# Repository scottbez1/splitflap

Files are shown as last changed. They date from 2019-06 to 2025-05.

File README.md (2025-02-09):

# Split-Flap Display

This is a DIY ESP32-based [split-flap display](https://en.wikipedia.org/wiki/Split-flap_display), optimized for easy assembly at home in small quantities but able to be scaled up to large affordable displays.

animated rendering






The [splitflap community Discord server](https://discord.com/invite/wgehm3PcrC) is the best place to keep up with the latest changes or ask questions about the project!

Want to help support development or just say "thanks"? Consider a one-time or monthly sponsorship:

| [:heart: Sponsor scottbez1 on GitHub](https://github.com/sponsors/scottbez1) |
|---|

<a href="https://www.youtube.com/watch?v=UAQJJAQSg_g" target="_blank">
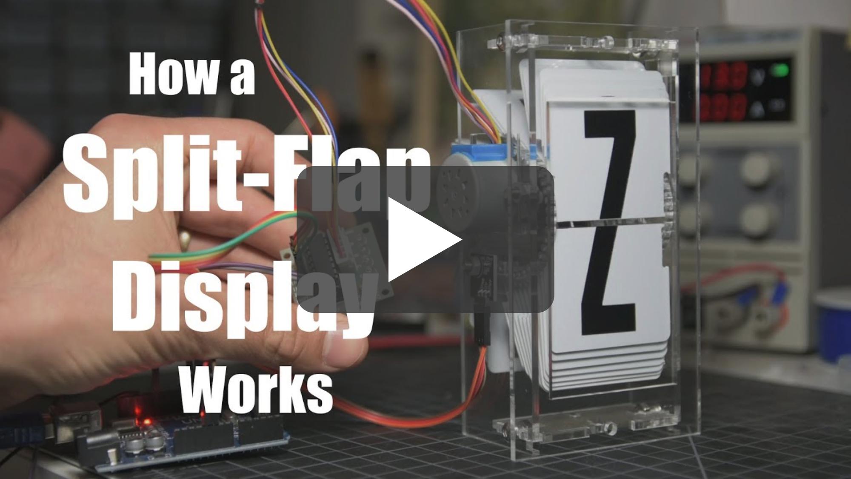
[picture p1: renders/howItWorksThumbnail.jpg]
  
</a>

**Using this project in a commercial setting or for paid client work?** Go right ahead - it's open source (just make sure to follow the terms of the Apache License)! I would, however, ask that you consider [sponsoring the project](https://github.com/sponsors/scottbez1). I've been developing and maintaining this project in my free time for over 10 years, and I'd love to continue working on it. Sponsorships allow me to pay for prototypes and development tools that make this project possible. Unlike pure software projects, every iteration has real hardware costs; sponsorships allow me to keep iterating and improving the project faster. Thank you!

# Current Status
[You can download the **latest stable releases** of the hardware designs from the official 'releases' page.](https://github.com/scottbez1/splitflap/releases)

Releases have been tested and used to produce working units, but as this is a continuously evolving open-source project, there may always be minor issues and/or incomplete documentation from time to time.

Here's a video of a large 108-module display powered by 18 Chainlink Driver boards and a Chainlink Base:

Video: animations on 108-module display (https://youtu.be/g9EPabcxBsM)

## Stable v2 Mechanical Release
As of 2025-01-19, the v2 refresh of the mechanical and sensor design is considered stable and recommended for new builds.

**Here's what's new in v2:**

- **52 flaps per module** for more character/symbol options
- **New printed flap design ("Epilogue")** with 52 flaps per set (see animation above), including several color-block flaps
- **Updated enclosure** and mechanical parts (laser-cut) to accomodate 52 flaps
  - Motor wires now exit downward for less awkward wiring!
- **New sensor PCB** that's easier to assemble and includes an LED for checking the magnet status
- **Software-configurable calibration** rather than mechanical sensor adjustment

**But many things are staying the same for easy upgrades/compatibility:**
- No change to flap dimensions!
- No changes to Chainlink Driver, Chainlink Buddy boards, or system architecture!
- 40-flap modules are still an officially supported option!
- Open source, as always!
- v0 parts (sensor kits) will continue to be stocked at Bezek Labs through mid-2025; don't worry if you haven't finished your build yet, the old sensor kits aren't going away for a little while!

I'd love to hear your thoughts and questions about this project, and happy to incorporate any feedback you might have into these designs! Please feel free (and encouraged) to [open GitHub issues](https://github.com/scottbez1/splitflap/issues/new), email me directly, reach out [on Bluesky](https://bsky.app/profile/scottbez1.bsky.social), and [get involved](https://github.com/scottbez1/splitflap/pulls) in the open source development and let's keep chatting and building together!

# Build Your Own
If you have any questions, please don't hesitate to ask in the [community Discord server](https://discord.gg/Hxnftc8PyW)!

* [**Documentation Index**](/docs/DocumentationIndex.md)
* [**Ordering guide (the "easy" route) v2**](/docs/v2/OrderingEasy.md)
* [**Comprehensive ordering guide**](/docs/v2/OrderingComplete.md)
* [**Chainlink Driver Electronics User Guide**](/docs/ElectronicsGuide.md)
* [**Assembly instructions v2**](/docs/v2/Assembly.md)
* [**Latest stable releases**](https://github.com/scottbez1/splitflap/releases)

# Table of Contents
- [Design Overview](#design-overview)
  - [Mechanical](#mechanical)
    - [Combined front panel (script)](#combined-front-panel-script)
    - [Flap font/sticker generator (script)](#flap-fontsticker-generator-script)
  - [Electronics](#electronics)
    - [Sensor PCBs](#sensor-pcbs-1-per-module)
    - [Chainlink Driver](#chainlink-driver-1-per-6-modules)
    - [Chainlink Buddy \[T-Display\]](#chainlink-buddy-t-display-1-for-entire-display)
    - [Advanced items](#advanced-items)
      - [Chainlink Buddy \[Breadboard\]](#chainlink-buddy-breadboard-1-for-entire-display-alternative-to-t-display)
      - [Chainlink Base](#chainlink-base-1-for-entire-display-large-displays)
    - [Older designs](#older-designs)
      - [Classic controller](#classic-controller-electronics-deprecated)
    + [Miscellaneous Tools](#miscellaneous-tools)
      - [3D Printed Tools](#3d-printed-tools)
      - [Chainlink Driver Tester](#chainlink-driver-tester)
  * [Code](#code)
    + [Firmware](#firmware)
    + [Computer Control Software](#computer-control-software)
- [Contributing/Modifying](#contributingmodifying)
  * [3D Design](#3d-design)
  * [Electronics Design](#electronics-design)

# Design Overview

## Mechanical
The mechanical/structural components are made from laser-cut 3mm MDF or acrylic, and held together with M4 bolts and nuts. The design is parametric and built using OpenSCAD. See below for more info on rendering/modifying the design.

You can view an interactive 3d model of the design [here](https://scottbez1.github.io/splitflap/embed.html?branch=master).

The v2 mechanical design officially supports variants with 52 flaps (perfect for use with the new ["Epilogue" printed flaps](https://bezeklabs.etsy.com/listing/1685633114/)) and 40 flaps. But you can always modify the design to customize it further.

### v2 (52-flap module option - recommended)
2d laser cut rendering

Instructions: [v2 assembly guide](/docs/v2/Assembly.md)

Module dimensions: 

Latest auto-generated (untested!) artifacts<sup>:warning:</sup>:
* For Ponoko 3mm MDF ([svg](https://s3.amazonaws.com/splitflap-artifacts/master/3d/3d_laser_vector-52-ponoko-3mm-mdf_1x.svg)) 
* For Ponoko 3mm acrylic ([svg](https://s3.amazonaws.com/splitflap-artifacts/master/3d/3d_laser_vector-52-ponoko-3mm-acrylic_1x.svg)) 
* For generic material (0.18mm kerf correction) ([svg](https://s3.amazonaws.com/splitflap-artifacts/master/3d/3d_laser_vector-52.svg))
* For Elecrow 3mm Wood ([zipped pdf](https://s3.amazonaws.com/splitflap-artifacts/master/3d/3d_laser_vector-52-elecrow-3mm-wood_1x.zip))
* For Elecrow 3mm Acrylic ([zipped pdf](https://s3.amazonaws.com/splitflap-artifacts/master/3d/3d_laser_vector-52-elecrow-3mm-acrylic_1x.zip))

<sup>:warning:</sup>For tested/stable/recommended artifacts, always use the [latest release](https://github.com/scottbez1/splitflap/releases) instead, as the links on this page will change over time.

### v2 (40-flap module option)
2d laser cut rendering

Instructions: [v2 assembly guide](/docs/v2/Assembly.md)

Module dimensions: 

Latest auto-generated (untested!) artifacts<sup>:warning:</sup>:
* For Ponoko 3mm MDF ([svg](https://s3.amazonaws.com/splitflap-artifacts/master/3d/3d_laser_vector-40-ponoko-3mm-mdf_1x.svg)) 
* For Ponoko 3mm acrylic ([svg](https://s3.amazonaws.com/splitflap-artifacts/master/3d/3d_laser_vector-40-ponoko-3mm-acrylic_1x.svg)) 
* For generic material (0.18mm kerf correction) ([svg](https://s3.amazonaws.com/splitflap-artifacts/master/3d/3d_laser_vector-52.svg))
* For Elecrow 3mm Wood ([zipped pdf](https://s3.amazonaws.com/splitflap-artifacts/master/3d/3d_laser_vector-40-elecrow-3mm-wood_1x.zip))
* For Elecrow 3mm Acrylic ([zipped pdf](https://s3.amazonaws.com/splitflap-artifacts/master/3d/3d_laser_vector-40-elecrow-3mm-acrylic_1x.zip))

<sup>:warning:</sup>For tested/stable/recommended artifacts, always use the [latest release](https://github.com/scottbez1/splitflap/releases) instead, as the links on this page will change over time.

### Combined front panel (script)
By default, the design will have a separate laser-cut faceplate for each individual module. For larger displays you may want to combine front panels into a single piece, and the repo has a script to help with this.

You can modify:
* Number of rows and columns
* Horizontal and vertical spacing/separation of modules
* Overall outer width and height of the panel

There are a lot of options; see the `--help` for explanations.

#### Example 1 - Laser cut 6x1

<a href="https://s3.amazonaws.com/splitflap-artifacts/master/3d/3d_front_panel-52-elecrow-3mm-acrylic-6x1.svg">

</a>

```
python3 3d/scripts/generate_combined_front_panel.py \
  --kerf-preset elecrow-3mm-acrylic \
  --num-flaps 52 \
  --cols 6 \
  --rows 1 \
  --spacing-x 0 \
  --spacing-y 0 \
  --frame-margin-x 0 \
  --frame-margin-y 0 \
  --center-mode module
```

#### Example 2 - CNC router 12x2, with frame margin
<a href="https://s3.amazonaws.com/splitflap-artifacts/master/3d/3d_front_panel-52-3.175-20x4margin-12x2.svg">

</a>

For CNC cutting, the script supports rendering a vector file optimized for thicker material (e.g. 6mm MDF) where only the bolt-holes will be through-cut. In this mode, the slots for the top/bottom enclosure pieces can be cut as ~4mm pockets so they aren't visible from the front face. The script automatically generates dog-bone shapes for these pocket cuts.

This example also demonstrates use of the --frame-margin-x and --frame-margin-y options to add an additional margin of 20mm horizontally and 4mm vertically to the front panel dimensions.

```
python3 3d/scripts/generate_combined_front_panel.py \
  --tool-diameter 3.175 \
  --num-flaps 52 \
  --cols 12 \
  --rows 2 \
  --spacing-x 0 \
  --spacing-y 0 \
  --frame-margin-x 20 \
  --frame-margin-y 4 \
  --center-mode module
```

### Flap font/sticker generator (script)
If you'd like to print your own flaps, or cut custom vinyl letter stickers, the project includes a script (`generate_fonts.py`) to generate vector design files, which is extremely configurable:

* Font for text
  * This is further customizable in `flap_fonts.scad` -- this is where font parameters are defined like the overall font scale, position offsets, and even per-character scale and position overrides in case you need to tweak particularly problematic letters (e.g. a really wide "W" or an "@" with too thin of a stroke).
* Character-set - which letters/numbers/symbols/colors are included and in what order
* Bleed - extends rendering past the borders of the flaps to compensate for slight misalignment of printing and cutting operations
* Keepout areas - option to highlight keepout violations for manual review, automatically clip them, or ignore them
* Rendering options:
    * Single-sided - useful for previewing how all letters will look on flaps
    * Front/back - for batch duplex printing, generate separate front-side and back-side files (e.g. sign shop printing on a flat sheet of PVC)
    * Side-by-side - for individual flap printing, each flap's front design is laid out side-by-side with its back design

There are a lot of options; see the `--help` for explanations.

#### Example 1 - Epilogue font, rendered in front+back pairs, default character set, 1mm bleed (for printing)

<a href="https://s3.amazonaws.com/splitflap-artifacts/master/3d/font_example-Epilogue-1mmBleed.svg">

</a>

```
python3 3d/scripts/generate_fonts.py \
  --mode side-by-side \
  --font Epilogue \
  --columns 4 \
  --bleed 1 \
  --fill
```

## Electronics
> [!NOTE]
> For small displays (up to 3 modules), you can skip the custom controller boards and use off-the-shelf ULN2003A driver
modules plugged into an Arduino Uno. This is [partially documented in the wiki](https://github.com/scottbez1/splitflap/wiki/Electronics#basic-prototyping-alternative-electronics-approach)
> but may require some additional tinkering to get it to work. _Help wanted: if you'd like to help improve these instructions,
> please reach out in the Discord server, thanks!_

The "Chainlink" electronics system is designed to support long chains of driver boards to control medium/large displays (up to 100+ split-flap modules).
It's also designed to be easy and cheap to order pre-assembled or build yourself, especially in higher
quantities, due to its simple BOM and surface-mount components.

To build a display, you'll need 3 different electronics:
* One **Sensor PCB** for every split-flap module
* One **Chainlink Driver** board for every 6 split-flap modules. This is what interfaces with the motors and sensors of each module. Chainlink Driver boards can be chained together to construct a large display.
* An ESP32 microcontroller board. There are a few options:
    * For small/medium displays, one of the **Chainlink Buddy** boards are recommended
        * **Chainlink Buddy [T-Display]**  holds a Lilygo T-Display ESP32 module which includes a built-in LCD and 2 buttons
        * **Chainlink Buddy [Breadboard]** makes it easy to connect a Chainlink Driver to a breadboard for prototyping, though you can also easily connect a Chainlink Driver to a breadboard with a few dupont wires.
    * For large displays, the **Chainlink Base** provides a number of advanced features: central
power management/distribution and fault monitoring, UART and RS-485 connections, configuration switches, and status LEDs.

### Sensor PCBs (1 per module)
Each module needs a hall-effect sensor for start-up calibration and fault monitoring. 

#### Sensors v2

<a href="https://s3.amazonaws.com/splitflap-artifacts/master/electronics-v2/panelized_sensor_smd-front-3d.png">

</a>
<a href="https://s3.amazonaws.com/splitflap-artifacts/master/electronics-v2/panelized_sensor_smd-back-3d.png">

</a>

<a href="https://s3.amazonaws.com/splitflap-artifacts/master/electronics-v2/sensor_smd-schematic.pdf">

</a>

New sensors for the v2 laser-cut hardware - these use surface mount components and are optimized for PCB assembly at JLCPCB. These new sensors are not compatible with v0.7 and older laser-cut hardware.

Packs of 6 sensors are [available mostly-assembled in the Bezek Labs store](https://bezeklabs.etsy.com/listing/1696745674),
and come with the right-angle pin headers and magnets you'll need. Purchases support continued development of this project.

Latest auto-generated (untested!) artifacts<sup>:warning:</sup>:

* Schematic [pdf](https://s3.amazonaws.com/splitflap-artifacts/master/electronics-v2/sensor_smd-schematic.pdf)
* Interactive BOM (for manual assembly) [interactive](https://s3.amazonaws.com/splitflap-artifacts/master/electronics-v2/sensor_smd-ibom.html)
* Fabrication files (single)
  * NOTE: PCBs must be 0.8mm! (rather than the more typical 1.6mm thickness)
  * PCB gerbers [zip](https://s3.amazonaws.com/splitflap-artifacts/master/electronics-v2/sensor_smd-jlc/gerbers.zip)
  * PCB BOM (for JLCPCB assembly) [csv](https://s3.amazonaws.com/splitflap-artifacts/master/electronics-v2/sensor_smd-jlc/bom.csv)
  * PCB CPL (for JLCPCB assembly) [csv](https://s3.amazonaws.com/splitflap-artifacts/master/electronics-v2/sensor_smd-jlc/pos.csv)
* Fabrication files (panelized)
  * NOTE: PCBs must be 0.8mm! (rather than the more typical 1.6mm thickness)
  * PCB gerbers [zip](https://s3.amazonaws.com/splitflap-artifacts/master/electronics-v2/sensor_smd-panelized-jlc/gerbers.zip)
  * PCB BOM (for JLCPCB assembly) [csv](https://s3.amazonaws.com/splitflap-artifacts/master/electronics-v2/sensor_smd-panelized-jlc/bom.csv)
  * PCB CPL (for JLCPCB assembly) [csv](https://s3.amazonaws.com/splitflap-artifacts/master/electronics-v2/sensor_smd-panelized-jlc/pos.csv)
* Purchase sensor kits in the US: [Bezek Labs](https://bezeklabs.etsy.com/listing/1696745674)

<sup>:warning:</sup>For tested/stable/recommended artifacts, always use the [latest release](https://github.com/scottbez1/splitflap/releases) instead, as the links on this page will change over time.

### Chainlink Driver (1 per 6 modules)
<a href="https://s3.amazonaws.com/splitflap-artifacts/master/electronics-chainlink/chainlinkDriver-3d.png">

</a>

Key features:
* Controls 6 split-flap modules per board
* Primarily SMD and all components (except the pin headers and motor connectors) are available in JLCPCB's parts library
for easy SMD/THT assembly
* Clock and latch lines are buffered on each board with a 74HC125 to support longer chains
* 2 bits of loopback error checking per board (connecting 2 spare output bits on output shift registers to 2 spare inputs) allows the controller
to validate data integrity up and down the whole chain
* Module order goes from right-to-left since this is intended to be installed and accessed from *behind* the modules

Chainlink Driver boards are [available mostly-assembled in the Bezek Labs store](https://bezeklabs.etsy.com/listing/1123280069/splitflap-chainlink-driver-v11),
and come with the additional connectors and ribbon cables you'll need. Purchases support continued development of this project.

More information on building and using Chainlink Drivers is available in the [Chainlink Driver User Guide](/docs/ElectronicsGuide.md).

Or if you'd like to order these directly from a fab, this design is optimized for assembly at JLCPCB, and files are automatically generated
for ordering *assembled* PCBs there. Or if you wish to assemble this board yourself instead of paying for assembly, 
you can view the [interactive BOM/placement tool](https://s3.amazonaws.com/splitflap-artifacts/master/electronics-chainlink/bom/chainlinkDriver-ibom.html)

Depending on available stock at JLCPCB, you may need to manually modify the BOM file to use alternative components, or regenerate the files
yourself using `export_jlcpcb.py` and specifying one or more `LCSC_ALT_*` field names to use a pre-selected alternative part number. See
the schematic for available pre-selected alternatives (check the symbol's properties/fields).

<a href="https://s3.amazonaws.com/splitflap-artifacts/master/electronics-chainlink/chainlinkDriver-schematic.pdf">

</a>

<a href="https://s3.amazonaws.com/splitflap-artifacts/master/electronics-chainlink/chainlinkDriver-pcb-raster.png">

</a>

Latest auto-generated (untested!) artifacts<sup>:warning:</sup>:

* Schematic [pdf](https://s3.amazonaws.com/splitflap-artifacts/master/electronics-chainlink/chainlinkDriver-schematic.pdf)
* PCB overview [pdf](https://s3.amazonaws.com/splitflap-artifacts/master/electronics-chainlink/chainlinkDriver-pcb-packet.pdf)
* PCB gerbers [zip](https://s3.amazonaws.com/splitflap-artifacts/master/electronics-chainlink/chainlinkDriver-jlc/gerbers.zip)
* PCB bom (for JLCPCB assembly) [csv](https://s3.amazonaws.com/splitflap-artifacts/master/electronics-chainlink/chainlinkDriver-jlc/bom.csv)
* PCB CPL (for JLCPCB assembly) [csv](https://s3.amazonaws.com/splitflap-artifacts/master/electronics-chainlink/chainlinkDriver-jlc/pos.csv)
* PCB bom (for manual assembly) [interactive](https://s3.amazonaws.com/splitflap-artifacts/master/electronics-chainlink/bom/chainlinkDriver-ibom.html)

<sup>:warning:</sup>For tested/stable/recommended artifacts, always use the [latest release](https://github.com/scottbez1/splitflap/releases) instead, as the links on this page will change over time.

### Chainlink Buddy \[T-Display\] (1 for entire display)
<a href="https://s3.amazonaws.com/splitflap-artifacts/master/electronics-chainlink-buddy-t-display/chainlinkBuddyTDisplay-3d.png">

</a>

The Chainlink Buddy \[T-Display\] is a convenient way to connect a T-Display ESP32 board (recommended microcontroller) to a chain
of Chainlink Drivers.

Key features:
* TTGO T-Display ESP32 module as the controller, which includes USB-C, color IPS LCD display and buttons
* Extra terminals for every pin of the T-Display allow you to connect any other peripherals to the ESP32 (the connection to the Chainlink Driver requires _only 4_ of the GPIOs)
* Optional barrel jack makes it easy to use a "wall wart" AC adapter/power-supply (since the Chainlink Driver only has screw terminals for power) -- plug in a 12V supply
and then run a wire from the onboard screw terminals to the Chainlink Driver's motor power screw terminals.
* Optional 5V regulator allows for powering the ESP32 without a USB connection, using the 12V motor power supply

Chainlink Buddy \[T-Display\] boards are [available in the Bezek Labs store](https://bezeklabs.etsy.com/listing/1109357786/splitflap-chainlink-buddy-t-display),
and come with the additional connectors you'll need. Purchases support continued development of this project. 

<a href="https://s3.amazonaws.com/splitflap-artifacts/master/electronics-chainlink-buddy-t-display/chainlinkBuddyTDisplay-schematic.pdf">

</a>

<a href="https://s3.amazonaws.com/splitflap-artifacts/master/electronics-chainlink-buddy-t-display/chainlinkBuddyTDisplay-pcb-raster.png">

</a>

Latest auto-generated (untested!) artifacts<sup>:warning:</sup>:

* Schematic [pdf](https://s3.amazonaws.com/splitflap-artifacts/master/electronics-chainlink-buddy-t-display/chainlinkBuddyTDisplay-schematic.pdf)
* PCB ([gerbers](https://s3.amazonaws.com/splitflap-artifacts/master/electronics-chainlink-buddy-t-display/chainlinkBuddyTDisplay-jlc/gerbers.zip) / [pdf](https://s3.amazonaws.com/splitflap-artifacts/master/electronics-chainlink-buddy-t-display/chainlinkBuddyTDisplay-pcb-packet.pdf))
* Panelized PCB ([gerbers](https://s3.amazonaws.com/splitflap-artifacts/master/electronics-chainlink-buddy-t-display/chainlinkBuddyTDisplay-panelized-jlc/gerbers.zip) / [pdf](https://s3.amazonaws.com/splitflap-artifacts/master/electronics-chainlink-buddy-t-display/chainlinkBuddyTDisplay-panelized-pcb-packet.pdf))
* PCB bom (for manual assembly) [interactive](https://s3.amazonaws.com/splitflap-artifacts/master/electronics-chainlink-buddy-t-display/bom/chainlinkBuddyTDisplay-ibom.html)

<sup>:warning:</sup>For tested/stable/recommended artifacts, always use the [latest release](https://github.com/scottbez1/splitflap/releases) instead, as the links on this page will change over time.

### Advanced items
#### Chainlink Buddy \[Breadboard\] (1 for entire display; alternative to T-Display)
<a href="https://s3.amazonaws.com/splitflap-artifacts/master/electronics-chainlink-buddy-breadboard/chainlinkBuddyBreadboard-3d.png">

</a>

The Chainlink Buddy \[Breadboard\] makes it easy to connect a Chainlink Driver to a breadboard for prototyping. You could use 5 dupont wires and have a
messy rats nest, or you could use a single ribbon cable and this slick breakout board.

Chainlink Buddy \[Breadboard\] boards are [available in the Bezek Labs store](https://bezeklabs.etsy.com/listing/1123863267/splitflap-chainlink-buddy-breadboard),
and come with the additional connectors you'll need. Purchases support continued development of this project. 

<a href="https://s3.amazonaws.com/splitflap-artifacts/master/electronics-chainlink-buddy-breadboard/chainlinkBuddyBreadboard-schematic.pdf">

</a>

<a href="https://s3.amazonaws.com/splitflap-artifacts/master/electronics-chainlink-buddy-breadboard/chainlinkBuddyBreadboard-pcb-raster.png">

</a>

Latest auto-generated (untested!) artifacts<sup>:warning:</sup>:

* Schematic [pdf](https://s3.amazonaws.com/splitflap-artifacts/master/electronics-chainlink-buddy-breadboard/chainlinkBuddyBreadboard-schematic.pdf)
* PCB ([gerbers](https://s3.amazonaws.com/splitflap-artifacts/master/electronics-chainlink-buddy-breadboard/chainlinkBuddyBreadboard-jlc/gerbers.zip) / [pdf](https://s3.amazonaws.com/splitflap-artifacts/master/electronics-chainlink-buddy-breadboard/chainlinkBuddyBreadboard-pcb-packet.pdf))
* Panelized PCB ([gerbers](https://s3.amazonaws.com/splitflap-artifacts/master/electronics-chainlink-buddy-breadboard/chainlinkBuddyBreadboard-panelized-jlc/gerbers.zip) / [pdf](https://s3.amazonaws.com/splitflap-artifacts/master/electronics-chainlink-buddy-breadboard/chainlinkBuddyBreadboard-panelized-pcb-packet.pdf))
* PCB bom (for manual assembly) [interactive](https://s3.amazonaws.com/splitflap-artifacts/master/electronics-chainlink-buddy-breadboard/bom/chainlinkBuddyBreadboard-ibom.html)

<sup>:warning:</sup>For tested/stable/recommended artifacts, always use the [latest release](https://github.com/scottbez1/splitflap/releases) instead, as the links on this page will change over time.

#### Chainlink Base (1 for entire display; large displays)
<a href="https://s3.amazonaws.com/splitflap-artifacts/master/electronics-chainlink-base/chainlinkBase-3d.png">

</a>

For larger displays, you should take additional care to make the hardware more robust to potential faults. The Chainlink Base is an experimental (but unsupported) controller design that adds some additional functionality. This has been tested and appears to work, but is not recommended for general use.

The Chainlink Base PCB is an optional alternative to a Chainlink Buddy, designed for particularly large displays.
It hosts the ESP32 and adds additional connectivity options (terminals for UART and RS485 serial) and
power distribution (independently-monitored power channels for multiple "zones" of Driver boards).

Key features:
* TTGO T-Display ESP32 module as the controller, which includes USB-C, color IPS LCD display and buttons
* Optional master relay output for 12V PSU control (5V relay, up to ~500mA coil current)
  * Future firmware will power on the 12V PSU after a startup self-test, and power off PSU in case of any faults
* 5 channels of independently monitored 12V switches for powering groups of Chainlink Driver boards (6-10A max per channel)
  * Depending on the motors you use, each channel may be able to power about 6 Chainlink Driver boards which is 36 splitflap modules
  * Each channel includes an automotive fuse holder for additional over-current protection
  * INA219 and shunt resistor provide high fidelity voltage and current monitoring 
  * Firmware will power on each channel after a startup self-test, and power off the channel in case of any faults
  * 3.3V output for powering many Chainlink Driver boards
* Flexible controller input power
  * USB power from the T-Display works by default, though external power is recommended for larger displays
  * Regulated 5V can be connected directly to the screw terminals, or
  * if you are using an always-on 12V PSU without a master relay, you can install a buck module and power the board from 12V using the 7-28V screw terminals

<a href="https://s3.amazonaws.com/splitflap-artifacts/master/electronics-chainlink-base/chainlinkBase-schematic.pdf">

</a>

<a href="https://s3.amazonaws.com/splitflap-artifacts/master/electronics-chainlink-base/chainlinkBase-pcb-raster.png">

</a>

Latest auto-generated (untested!) artifacts<sup>:warning:</sup>:

* Schematic [pdf](https://s3.amazonaws.com/splitflap-artifacts/master/electronics-chainlink-base/chainlinkBase-schematic.pdf)
* PCB overview [pdf](https://s3.amazonaws.com/splitflap-artifacts/master/electronics-chainlink-base/chainlinkBase-pcb-packet.pdf)
* PCB gerbers [zip](https://s3.amazonaws.com/splitflap-artifacts/master/electronics-chainlink-base/chainlinkBase-jlc/gerbers.zip)
* PCB bom (for manual assembly) [interactive](https://s3.amazonaws.com/splitflap-artifacts/master/electronics-chainlink-base/bom/chainlinkBase-ibom.html)

<sup>:warning:</sup>There are currently no stable releases of this board, and none are planned. Some past variants of this board have been used, to some success, but it is not considered an
officially supported design

## Older designs
### Classic Controller Electronics (deprecated)
The Classic driver board is deprecated and unsupported.

The Classic controller board was designed to plug into an Arduino like a shield, and could control 4 stepper motors.
Up to 3 driver boards could be chained together, for up to 12 modules controlled by a single Arduino.

The driver uses 2 MIC5842 low-side shift-register drivers, with built-in transient-suppression diodes, to control the motors, and a 74HC165 shift register to read from 4 hall-effect magnetic home position sensors.
There are optional WS2812B RGB LEDs which can be used to indicate the status of each of the 4 channels.

### Miscellaneous Tools

#### 3D Printed Tools
The project also includes a number of optional 3D printed designs to make assembly easier. These include:

* [a flap scoring jig](3d/tools/scoring_jig.scad) for precisely marking the cut point when splitting CR80 cards
* [a flap punch jig](3d/tools/punch_jig.scad) for aligning the punch when making the pin cutouts on either side of a flap
* [a flap container](3d/tools/flap_container.scad) for storing and organizing stacks of completed flaps

All of these designs are parametric and customizable within OpenSCAD. To print them, open up the relevant file in OpenSCAD and use `File -> Export -> Export as STL` to render the design as an STL file for your slicer.

#### Chainlink Driver Tester
<a href="https://s3.amazonaws.com/splitflap-artifacts/master/electronics-chainlink-tester/chainlinkDriverTester-3d.png">

</a>

This is not likely to be useful unless you're planning to manufacture dozens to hundreds of Chainlink Driver boards, but the Chainlink Driver Tester is a complete testbed
for Chainlink Driver boards as they come assembled by the PCBA fabricator.

This is currently under very active development.

Key features:
* TTGO T-Display (ESP32) controller, screen, and buttons for controlling tests and reporting results
* Pogo-pins for all connectors on the Chainlink Driver board-under-test (screw terminals, sensor pin headers, and motor connectors)
* 12V switch to supply motor power to the board-under-test, with automotive fuse and INA219 voltage/current monitoring (based on the Chainlink Base channel switch design)
* Separate 3.3V supply for the board-under-test, protected with a polyfuse, should avoid browning out the Tester's MCU in case of 3.3V short-circuits
* Motor and sensor connections are broken out from the pogo-pins for a full closed-loop hardware test
* Screw terminals to chain another Chainlink Driver (not under test) to validate that chained outputs work on the board-under-test
* MCP23017 GPIO expander with 8 GPIO pins exposed via headers for future expansion inputs
* Large cutout allows a barcode scanner or camera to be aimed at the bottom of the board-under-test for tracking serial numbers.
* Buzzer option for audible pass/fail feedback

<a href="https://s3.amazonaws.com/splitflap-artifacts/master/electronics-chainlink-tester/chainlinkDriverTester-schematic.pdf">

</a>

<a href="https://s3.amazonaws.com/splitflap-artifacts/master/electronics-chainlink-tester/chainlinkDriverTester-pcb-raster.png">

</a>

Latest auto-generated (untested!) artifacts<sup>:warning:</sup>:

* Schematic [pdf](https://s3.amazonaws.com/splitflap-artifacts/master/electronics-chainlink-tester/chainlinkDriverTester-schematic.pdf)
* PCB overview [pdf](https://s3.amazonaws.com/splitflap-artifacts/master/electronics-chainlink-tester/chainlinkDriverTester-pcb-packet.pdf)
* PCB gerbers [zip](https://s3.amazonaws.com/splitflap-artifacts/master/electronics-chainlink-tester/chainlinkDriverTester-jlc/gerbers.zip)
* PCB bom (for manual assembly) [interactive](https://s3.amazonaws.com/splitflap-artifacts/master/electronics-chainlink-tester/bom/chainlinkDriverTester-ibom.html)

<sup>:warning:</sup>There are currently no stable releases of this board, and there may never be as it is a niche production tool, not an end product. If you
need this tool, you are likely actively involved in development and should understand the revision history and current status of development enough to make
an informed decision about which revision(s) to use.

## Code
### Firmware
The driver firmware is written using PlatformIO with the Arduino framework and is available at [`firmware/`](firmware/). 

The firmware implements a closed-loop controller that accepts letters as input over USB serial and drives the stepper motors using a precomputed acceleration ramp for smooth control. The firmware automatically calibrates the spool position at startup, using the hall-effect magnetic sensor, and will automatically recalibrate itself if it ever detects that the spool position has gotten out of sync. If a commanded rotation is expected to bring the spool past the "home" position, it will confirm that the sensor is triggered neither too early nor too late; otherwise it will search for the "home" position to get in sync before continuing to the desired letter.

### Serial protocol
In order for a computer to communicate with the splitflap, it appears as a USB serial device.

However, usage of Arduino’s `Serial` is strictly forbidden, and instead a `logger` abstraction is provided for sending basic text debug logs. Other data is transferred in a structured way, described below.

This allows flexibility in the format of data transferred over serial, and in fact the splitflap provides 2 different serial modes that serve different purposes.

#### Plaintext mode

By default, it starts in “plaintext” mode, which is developer-friendly and you’re probably familiar with if you’ve opened a serial monitor with the splitflap connected:
```
{"type":"init", "num_modules":6}
```

However, this isn’t great for programmatically configuring or receiving updates from the splitflap, so instead the firmware offers a programmatic interface using a binary protocol based on Google’s Protobuf standard.

#### Protobuf (binary/programmatic) mode

The protobuf-based binary serial mode is a compact and flexible way to transfer structured data from the host computer to the splitflap and vice-versa.

##### Benefits of protobuf
protobuf provides several benefits over other encoding mechanisms like JSON:

1. Well-defined schema. If you’re curious about the format of data to expect or send, you just need to check the protobuf file
2. Code generation. Instead of hand-writing JSON parsers every time the data changes, protobuf provides code generation of the encoding and decoding logic, and data-structures. Splitflap uses nanopb to generate C structs based off the schema, and all the code for encoding/decoding that data from the binary format.
3. Relatively compact/efficient wire encoding. It’s not a primary goal in this project, but the binary wire encoding is generally fairly compact, due to omitting default/unspecified fields, using variable length encodings, etc. It’s certainly much more compact than JSON which uses strings to describe every field in every message.
4. Backwards/forwards compatibility. Not super relevant to this project, but many common schema changes are backwards and forwards compatible, meaning an older client or a newer client will be able to handle them gracefully.

##### Disadvantages of protobuf

1. Not human-readable. This makes it much harder to debug, as you need something that can interpret messages. Since they’re binary, viewing anything in a terminal directly will be fruitless.
2. Not self-describing. If you come across a JSON document, you can generally tell what it means because fields have string names/labels describing their contents. Protobuf has no such thing (it uses integer field numbers, which does make renaming fields easier) so you need to have a copy of the schema (.proto file - and you’d better hope it matches the data!) in order to understand an encoded message.

This is why the splitflap defaults to plaintext mode to make basic validation/debugging easier.

##### How it works
Protobuf messages are encoded to their binary wire format and a CRC32 checksum appended. Then that entire binary string is COBS encoded into a packet, and delimited/framed by 0 (NULL) bytes when sent over serial. This provides a basic packet-based interface with integrity checks (rather than the raw, stream-based interface of a serial connection).

The splitflap automatically switches to binary protobuf mode when it receives a 0 byte.

### Computer Control Software
The display can be controlled by a computer connected to the ESP32 over USB serial. If you've built a display and want to test it out, check out the web-based demo [here](https://scottbez1.github.io/splitflap) which will connect to your display using USB - no applications/installation necessary!

The firmware supports a plaintext serial mode (enabled by default) for ease of testing, and a protobuf-based binary mode used by the software libraries for enhanced programmatic control and feedback.

You can find example Typescript and Python libraries in the [`software/chainlink`](software/chainlink) folder.

# Contributing/Modifying

Looking to make some modifications or play around with the design on your local machine? Jump right in! Note that all of the scripts and automation are developed for Ubuntu. Mac OS support is planned,
but not currently implemented (but feel free to open a PR if you want to help!).

## 3D Design

The main design file is [`3d/splitflap.scad`](3d/splitflap.scad)

You'll need a recent version of OpenSCAD (e.g. 2015-03), which may need to be installed through the PPA:
`sudo add-apt-repository ppa:openscad/releases`

In general, solid objects such as the enclosure sides or spool components are built from 2d primitives and then extruded to the appropriate thickness for 3d rendering, rather than using 3d primitives. This simplifies the design without losing expressiveness; the perpendicular laser cut beam doesn't allow for cuts that vary in the Z dimension anyway.

Note that while the design is parameterized and many values may be tweaked, there is currently no error checking for invalid parameters or combinations of parameters. Please take care to validate the design if you change any parameters. For instance, while most of the design will adjust to a changed `num_modules` value, certain values may cause some elements to intersect with other elements or protrude beyond their expected dimensions.

### Rendering
#### Laser-cut vector files
The design can be rendered to 2d for laser cutting by running [`3d/scripts/generate_2d.py [--panelize <number>]`](3d/scripts/generate_2d.py), which outputs to `3d/build/laser_parts/combined.svg`. The optional `--panelize` argument allows for rendering a panel of modules in a single SVG, for bulk laser-cutting.

Internally, the design uses a `projection_renderer` module ([`3d/projection_renderer.scad`](3d/projection_renderer.scad)), which takes a list of child elements to render, and depending on the `render_index` renders a single child at a time. It also _adds_ material to each shape to account for the kerf that will be cut away by the laser.

The [`generate_2d.py`](3d/scripts/generate_2d.py) script interacts with the `projection_renderer` module by first using it to determine the number of subcomponents to render, then runs OpenSCAD to export each component to an SVG file. It does some post-processing on the SVG output (notably adds "mm" to the document dimensions), and then combines all components into the single `combined.svg` output.

Once the `combined.svg` file is generated, you'll want to double-check there aren't any redundant cut lines that are shared by multiple adjacent pieces, to save time/cost when cutting. They should be detected automatically (and highlighted in red in the rendering above), but it doesn't hurt to double-check. In Inkscape, select the "Edit paths by nodes" tool and select an edge to delete - the endpoints should turn blue. Then click "Delete segment between two non-endpoint nodes", and repeat this for all other redundant cut lines.

#### Animated gif
The design can be rendered to a rotating 3d animated gif (seen above) by running [`3d/scripts/generate_gif.py`](3d/scripts/generate_gif.py), which outputs to `3d/build/animation/animation.gif`

The `generate_gif.py` script runs multiple OpenSCAD instances in parallel to render the design from 360 degrees to individual png frames, which are then combined into the final gif animation. As part of building the animation, `generate_gif.py` renders the design with multiple configurations (opaque enclosure, see-through enclosure, no-enclosure and no flaps) by setting the `render_enclosure` and `render_flaps` variables.

#### STL models/web viewer
The design can be rendered to a series of STL files (one per color used in the model) in order to be displayed in an [interactive web-based 3d viewer](https://scottbez1.github.io/splitflap/). Similar to the `projection_renderer` used to render individual components for laser-cutting, the [ColoredStlExporter](3d/scripts/colored_stl_exporter.py) detects all the colors used in the model and renders them one-by-one to separate STL files, along with a manifest that maps each STL file to its RGB color. The STL files and manifest are loaded using three.js to display an interactive model on a web site using WebGL. See this blog post for more details on how the export and three.js renderer work: [OpenSCAD Rendering Tricks, Part 3: Web viewer](http://scottbezek.blogspot.com/2016/08/openscad-rendering-tricks-part-3-web.html).

## Electronics Design
All of the electronics are developed using KiCad 5. Panelization is provided by [KiKit](https://github.com/yaqwsx/KiKit) and gerber/BOM generation is provided by [KiBot](https://github.com/INTI-CMNB/KiBot).

### Rendering
The mechanical and electrical design renderings and links above are automatically updated on every commit with the latest rendering. See this blog post for more details on how that works: [Automated KiCad, OpenSCAD rendering using Travis CI](http://scottbezek.blogspot.com/2016/04/automated-kicad-openscad-rendering.html).

The PCB layout can be rendered to an svg or png (seen above) by running [`electronics/scripts/generate_svg.py file.kicad_pcb`](electronics/scripts/generate_svg.py).
This uses KiCad's [Python scripting API](https://docs.kicad-pcb.org/doxygen/md_Documentation_development_pcbnew-plugins.html)
to render several layers to individual svg files, manipulates them to apply color and opacity settings, and then merges them to a single svg.
For additional details, see this blog post: [Scripting KiCad Pcbnew exports](http://scottbezek.blogspot.com/2016/04/scripting-kicad-pcbnew-exports.html).

For reviewing the design, a pdf packet with copper, silkscreen, and drill info can be produced by running [`electronics/scripts/generate_pdf.py file.kicad_pcb`](electronics/scripts/generate_pdf.py).

Gerber files for fabrication can be exported by running [`electronics/scripts/generate_gerber.py file.kicad_pcb`](electronics/scripts/generate_gerber.py).
This generates gerber files and an Excellon drill file with Seeed Studio's [naming conventions](http://support.seeedstudio.com/knowledgebase/articles/1176532-how-to-generate-the-gerber-manufacturing-files) and produces a `.zip` which can be sent for fabrication.

EESchema isn't easily scriptable, so to export the schematic [`electronics/scripts/export_schematic.py`](electronics/scripts/export_schematic.py) starts an X Virtual Frame Buffer (Xvfb) and open the `eeschema` GUI within that virtual display, and then send a series of hardcoded key presses via `xdotool` to interact with the GUI and click through the dialogs. This is very fragile but seems to work ok for now. For additional details, see this blog post: [Using UI automation to export KiCad schematics](http://scottbezek.blogspot.com/2016/04/automated-kicad-schematic-export.html).

# License
I'd love to hear your thoughts and questions about this project, and happy to incorporate any feedback you might have into these designs! Please feel free (and encouraged) to [open GitHub issues](https://github.com/scottbez1/splitflap/issues/new), email me directly, reach out [on Twitter](https://twitter.com/scottbez1), and [get involved](https://github.com/scottbez1/splitflap/pulls) in the open source development and let's keep chatting and building together!

This project is licensed under Apache v2 (see [LICENSE.txt](LICENSE.txt)).

    Copyright 2015-2025 Scott Bezek and the splitflap contributors
    
    Licensed under the Apache License, Version 2.0 (the "License");
    you may not use this file except in compliance with the License.
    You may obtain a copy of the License at
    
        http://www.apache.org/licenses/LICENSE-2.0
    
    Unless required by applicable law or agreed to in writing, software
    distributed under the License is distributed on an "AS IS" BASIS,
    WITHOUT WARRANTIES OR CONDITIONS OF ANY KIND, either express or implied.
    See the License for the specific language governing permissions and
    limitations under the License.

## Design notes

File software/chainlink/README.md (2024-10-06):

# Chainlink software

## Python Code

Run the demo by installing the requirement dependencies outlined in the [requirements.txt](./requirements.txt).

### Running the demo

The demo will just send multiple different words to the splitflap board. You may start the demo by executing:

```bash
python demo.py
```

You may get an output looking like this:

```bash
Available ports:
[ 0] /dev/ttyACM0 - USB Single Serial
[ 1] /dev/ttyAMA0 - ttyAMA0
```

Select which port the demo script should execute.

Now the demo should send different words to the splitflap board with short breaks in between them.

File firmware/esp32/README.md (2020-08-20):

This folder contains extra source files to replace the main (Splitflap.ino)
source file when building for ESP32 via PlatformIO. See the "esp32"
enviornment definition in platformio.ini for more info about how these files
are included.

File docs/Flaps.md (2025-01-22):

[<< Back to Documentation Index](../DocumentationIndex.md)

# About flaps
Flap dimensions

The flaps in this design are based around standard credit-card sized PVC cards (aka CR80). Each flap is 1/2 of a card, and has notches cut of the sides to create a "pin" that fits into the flap spool and allows it to flip freely.

There are either 52 flaps (v2) or 40 flaps (v0) for every module, so for a small 6-character display that will be a total of 312 flaps (v2) or 240 flaps (v0) that need to be cut and have letters applied to them if you take the full DIY approach.

Because there are so many flaps required for larger displays, I've also had custom flaps (both blank and pre-printed) manufactured that I sell in the [Bezek Labs Etsy store](https://bezeklabs.etsy.com/), which can save a lot of time and helps support continued development of this project.

# Option 1: Pre-printed flaps
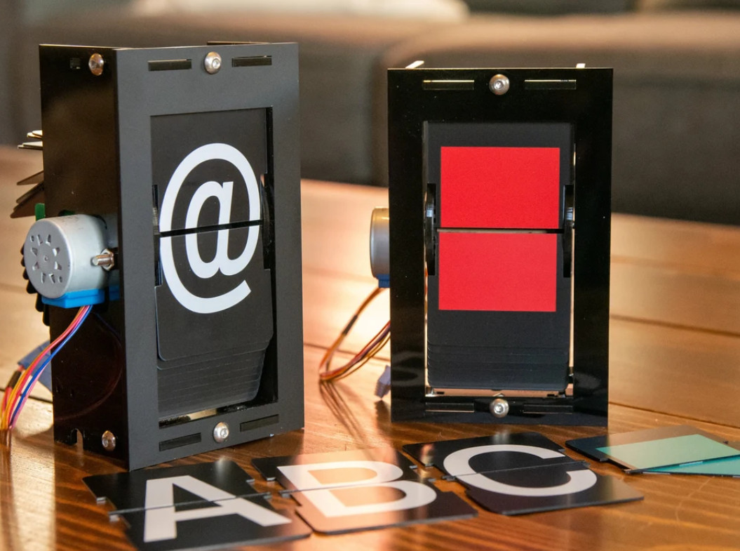
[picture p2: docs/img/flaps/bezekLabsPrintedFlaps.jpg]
Bezek Labs professionally cut blank white flaps


If you'd like to save the most time, I sell [packs of profesionally cut and printed flaps](https://www.etsy.com/listing/1685633114), ready to install into your split-flap display. THese are designed for v2 displays.

This is definitely the priciest option since they're completely custom for this project (a single pack requires 52 different printed designs!), but they look great and will hold up well to long-term use.

Available in <a href="https://www.etsy.com/listing/1685633114">1-packs, 6-packs, and 24-packs in the Bezek Labs Etsy store</a>.

<a href="https://www.etsy.com/listing/1685633114">
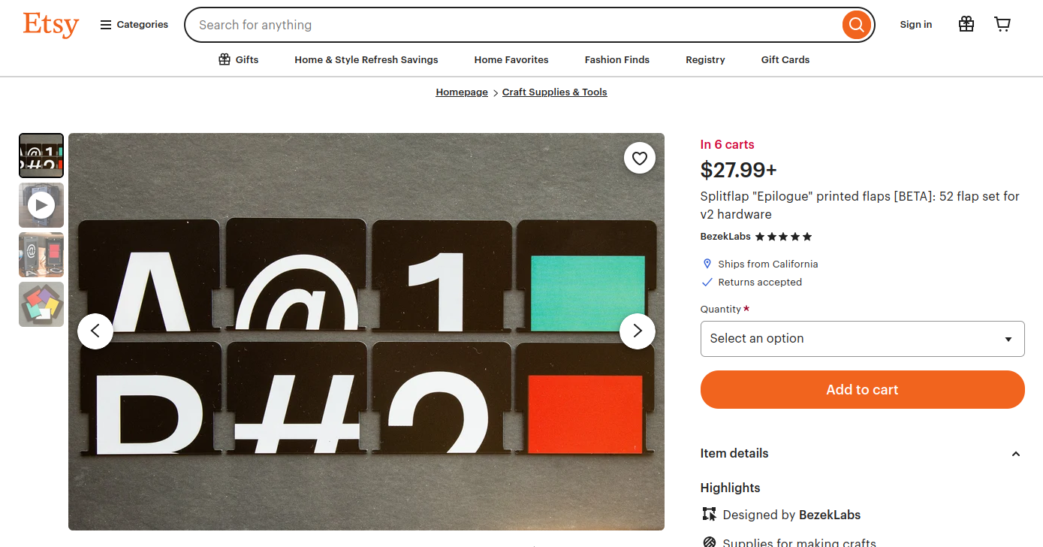
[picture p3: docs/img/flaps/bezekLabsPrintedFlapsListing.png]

</a>

[^ Up to top](#about-flaps)

[<< Back to Documentation Index](../DocumentationIndex.md)

# Option 2: Pre-cut blank flaps
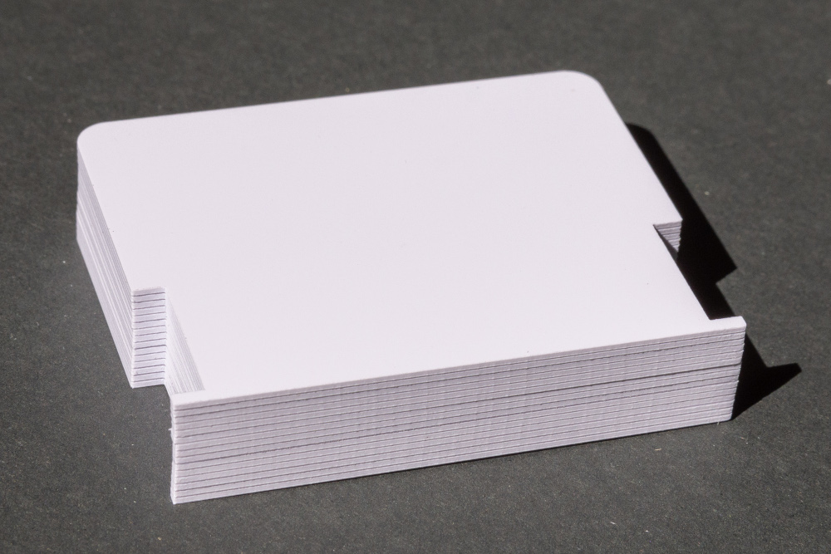
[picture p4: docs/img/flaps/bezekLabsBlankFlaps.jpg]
Bezek Labs professionally cut blank white flaps

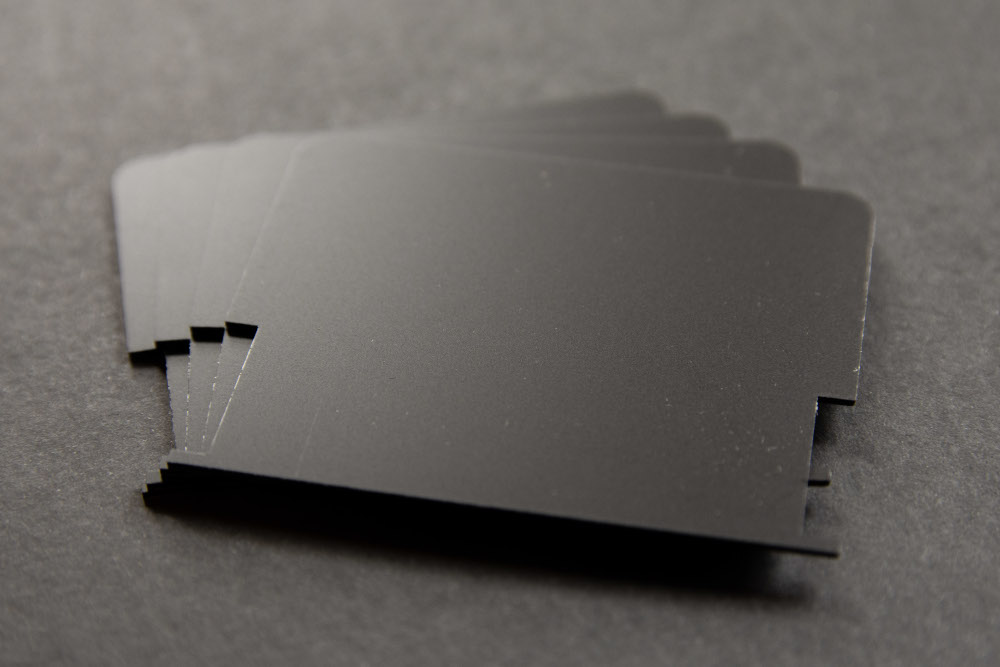
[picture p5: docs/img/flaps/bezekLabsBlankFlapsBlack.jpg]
Bezek Labs professionally cut blank black flaps


An intermediate option is to buy pre-cut blank flaps, and then apply letter stickers of your choice to them. This saves the hassle of cutting/punching every flap, but still involves some tedious work to apply stickers to every flap.

I sell packs of blank flaps in the <a href="https://bezeklabs.etsy.com/listing/979720975">Bezek Labs Etsy store</a>, available in glossy white or matte black.

<a href="https://bezeklabs.etsy.com/listing/979720975">
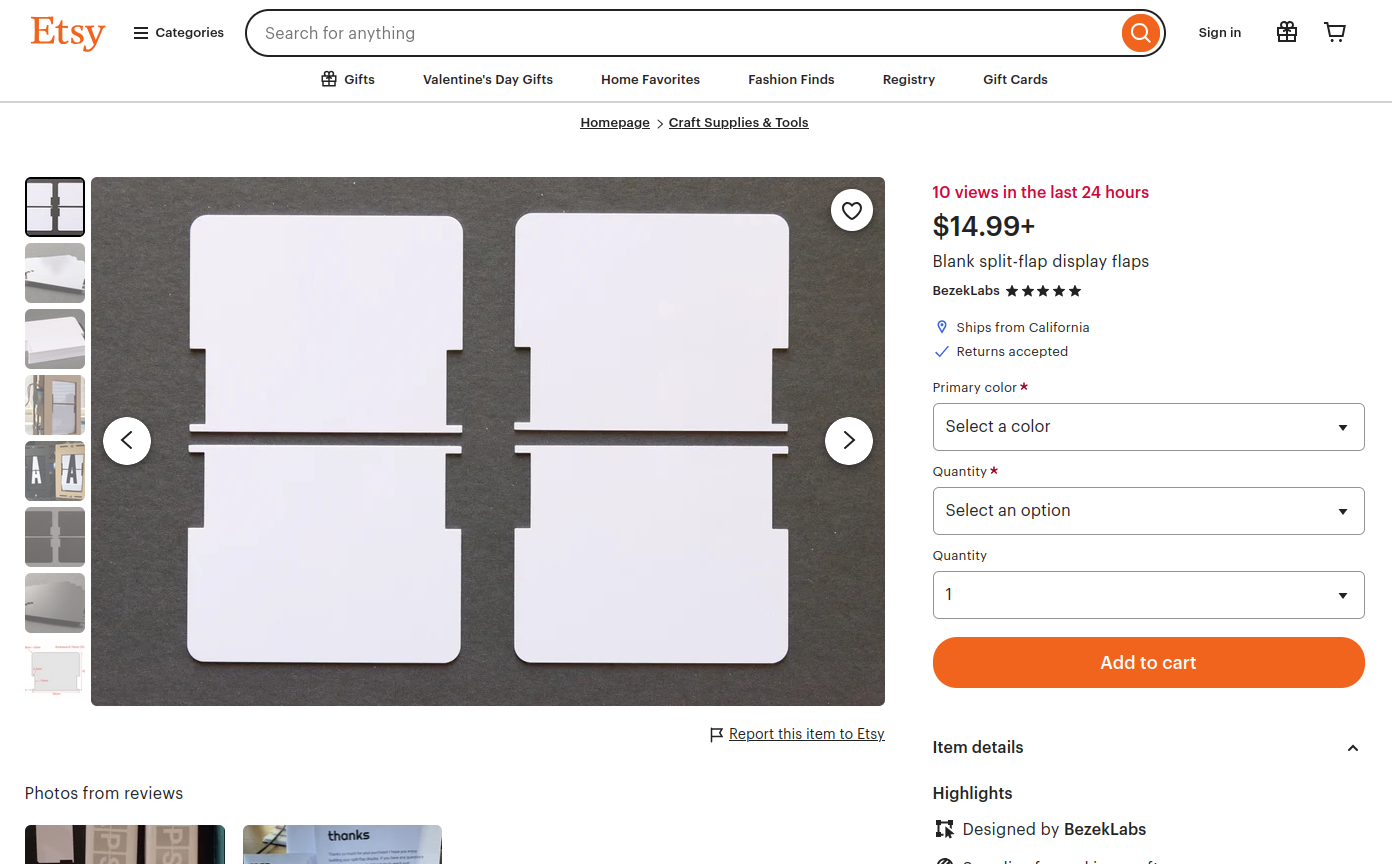
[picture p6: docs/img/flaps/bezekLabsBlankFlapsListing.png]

</a>

You'll need to [apply letter stickers](#33-apply-letter-stickers) to the blank flaps.

[^ Up to top](#about-flaps)

[<< Back to Documentation Index](../DocumentationIndex.md)

# Option 3: DIY flaps
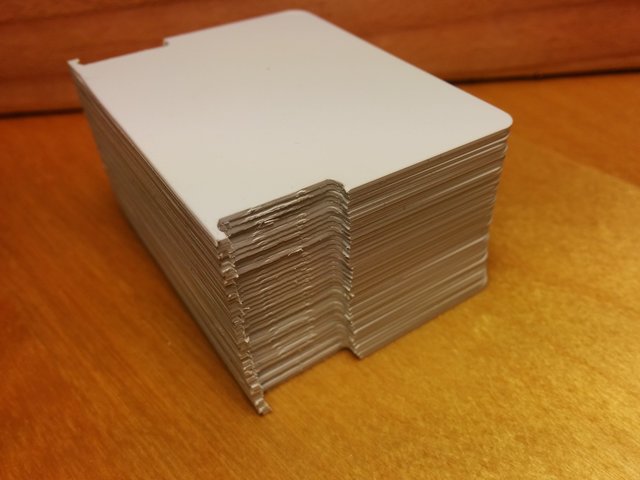
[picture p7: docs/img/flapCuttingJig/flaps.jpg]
flap with notches cut by hand


If you want the full DIY experience, the flaps can be created by first cutting a CR80 card in half, then punching notches out of each side of the half cards, and finally applying letter stickers to them.

If this sounds tedious, I'll admit that it is, but it's how I built the first few splitflap modules.

## 3.1 Build a flap cutting jig

The notch cut-outs need to be done consistently for all 40 flaps, so we'll first create a jig for the [badge slot punch](http://www.amazon.com/gp/product/B009YDRRB4) to hold a flap in a precise position while cutting it.

The jig can either be created by hand using a PVC card, or, if you have a 3d printer, can simply be printed ([see below](#3d-printing-a-jig))

### 3d printing a jig

If you have a 3d printer, you can print a jig model rather than creating the jig by hand. It will look like this:

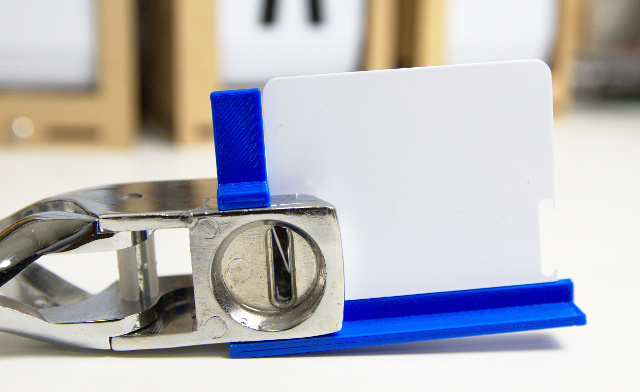
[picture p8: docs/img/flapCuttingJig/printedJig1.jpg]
3d-printed jig


To print this jig, open [3d/punch_jig.scad](https://github.com/scottbez1/splitflap/blob/master/3d/tools/punch_jig.scad), render it and export to an STL file. You can use your slicer of choice to prepare the model for 3d printing.

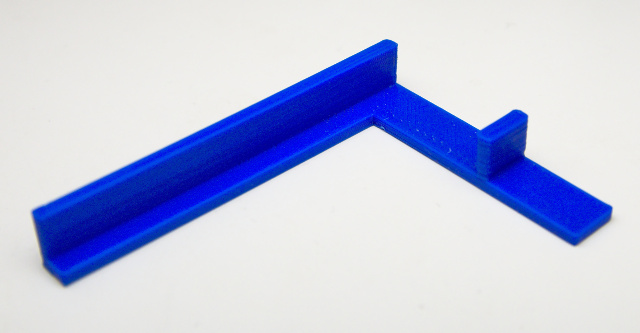
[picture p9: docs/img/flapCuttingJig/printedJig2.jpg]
3d-rinted jig
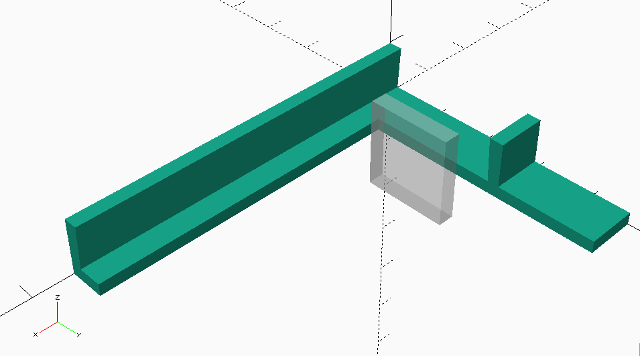
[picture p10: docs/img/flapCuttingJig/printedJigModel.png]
Model of the 3d printed jig
 

(Thanks to [@SilentM4X](https://twitter.com/SilentM4X) for the [idea to print the jig](https://twitter.com/SilentM4X/status/974688413373870085)!)

### Creating a jig by hand

The jig created from a PVC card will eventually look like this:

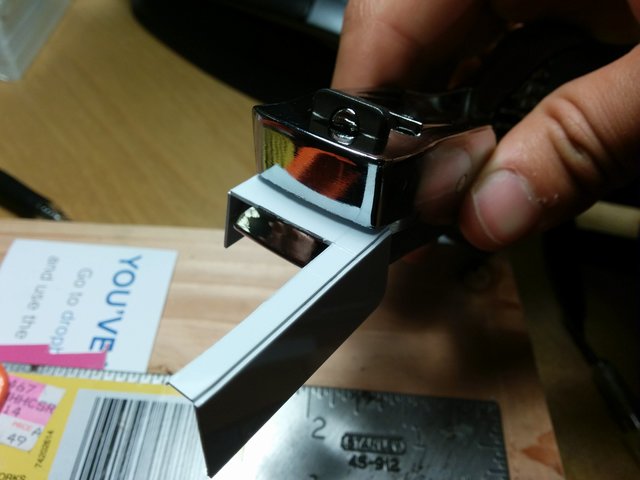
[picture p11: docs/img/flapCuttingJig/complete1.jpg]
badge punch with alignment jig


To build this, start by taking half a PVC card (or any spare ID or credit card you may have laying around), insert it all the way to the back of the punch, and punch a slot in the center. While the punch is still engaged (holding the card in place), take your X-Acto knife and lightly score the top of the card along the outer edges of the punch (just enough to mark it).

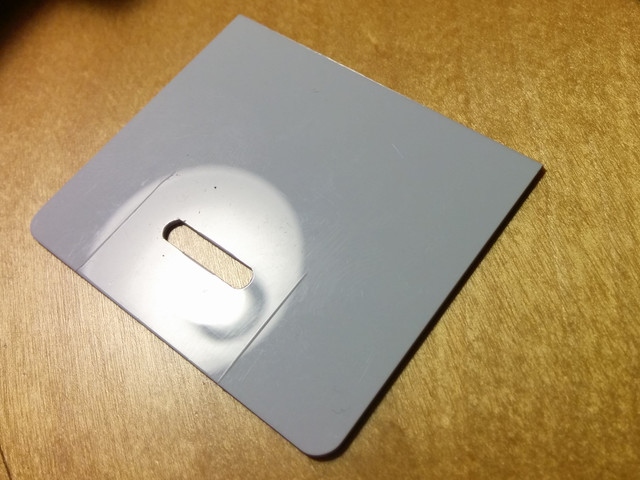
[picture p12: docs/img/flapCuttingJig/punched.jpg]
punched card with marked edges


Take the card and a ruler and score it along the 2 lines you marked (cut about 1/3 of the way through the card thickness, but err on the side of cutting less). Then align the ruler with the flat edge of the punched slot nearest the card edge and use the knife to fully cut the card from the right side of the punched slot to the right edge of the card. Then turn the ruler 90 degrees and place it ~1-2mm outside the left side of the punched slot (this determines the thickness of the flap "pin") and cut from the bottom edge of the slot to the top of the card. 

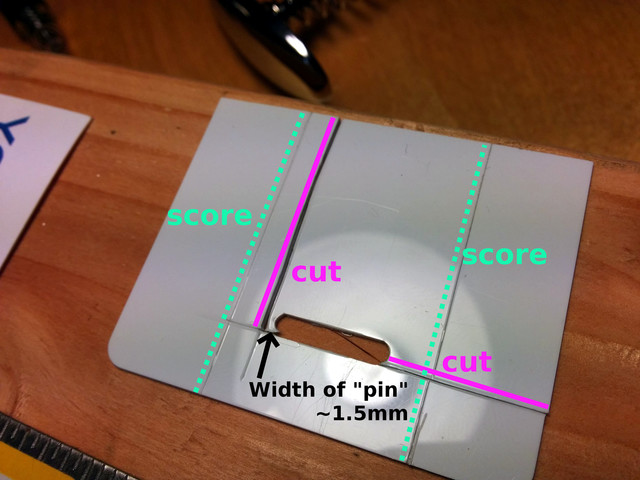
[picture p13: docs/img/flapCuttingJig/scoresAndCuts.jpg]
punched card with scores and cuts


Connect those 2 cuts so that the upper right section of the card can be removed entirely:

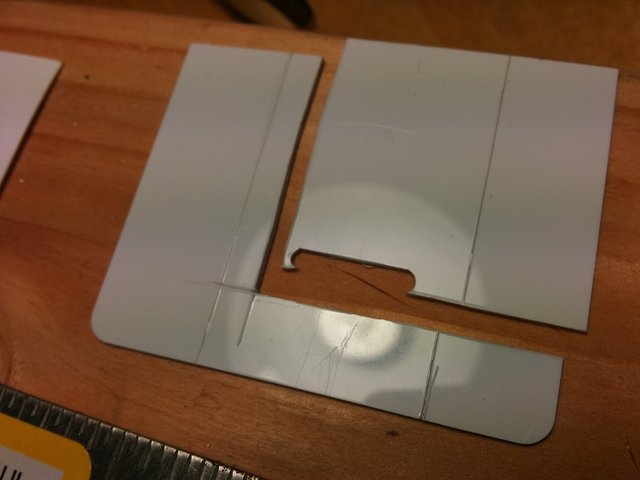
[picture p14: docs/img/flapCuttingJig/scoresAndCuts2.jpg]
punched card with section moved


Fold the card 90 degrees away from you along the 2 scored edges:

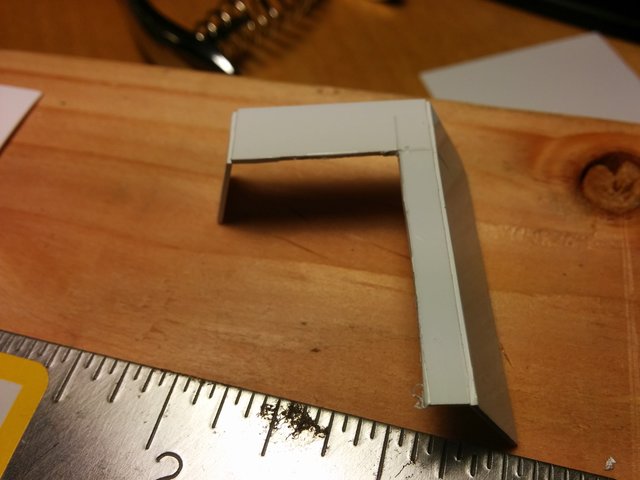
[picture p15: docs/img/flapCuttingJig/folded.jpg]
folded jig


Insert the jig into the punch (the same orientation you originally punched it), and tape it into place:

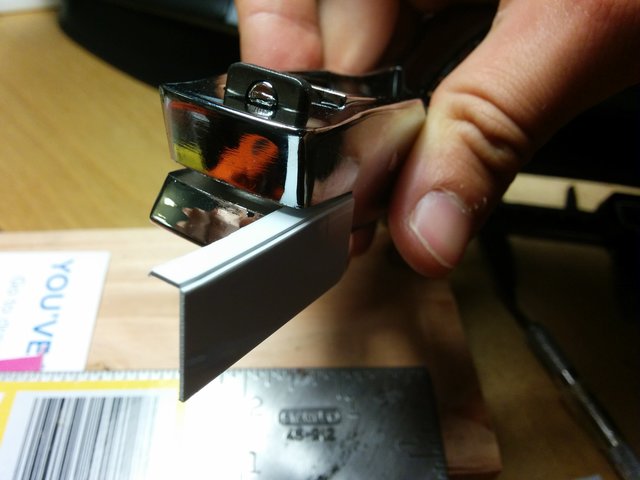
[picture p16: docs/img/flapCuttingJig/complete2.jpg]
folded jig in punch 2
folded jig in punch 

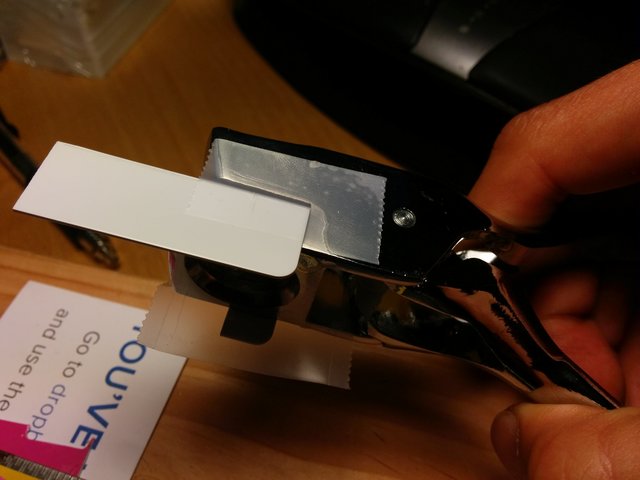
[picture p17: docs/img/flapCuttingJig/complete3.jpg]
folded jig in punch 3
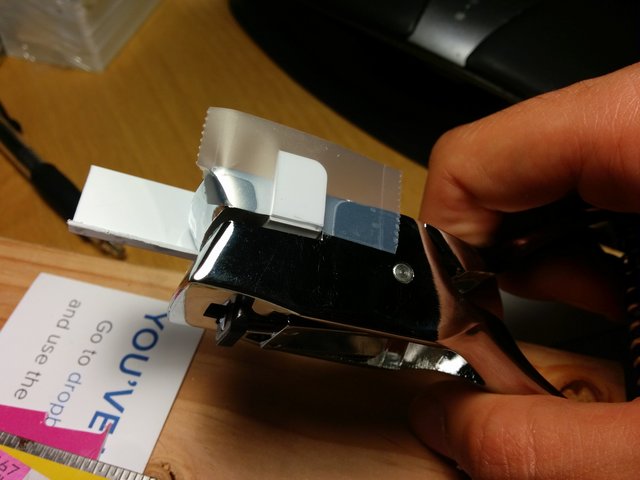
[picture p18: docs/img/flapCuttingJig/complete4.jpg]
folded jig in punch 4
 

Your flap-cutting jig is complete!

[^ Up to top](#about-flaps)

[<< Back to Documentation Index](../DocumentationIndex.md)

## 3.2 Cut flaps

To cut the flaps from CR80 PVC cards, they first need to be cut in half. You could probably do this with a paper guillotine, but I don't own one so I made a jig to score them with a utility knife and then snap them in half.

Start by putting 3 nails into a scrap piece of wood to hold the card in place:

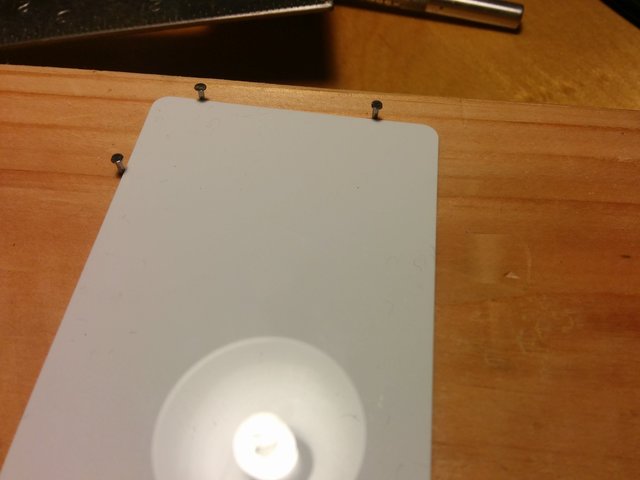
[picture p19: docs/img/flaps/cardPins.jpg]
nails to align card


Then, on either side of the working area, place a card or two (I used a PVC card plus a business card) to elevate a ruler which will be clamped in place as a straight edge for scoring.

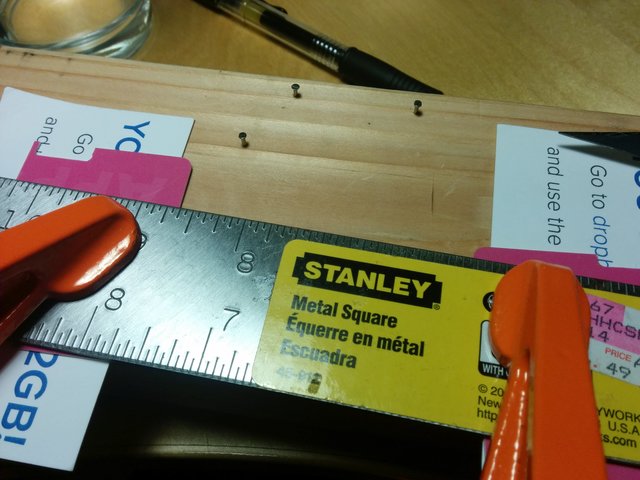
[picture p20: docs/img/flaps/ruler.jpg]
ruler placement


Make sure the ruler is clamped exactly 1/2 card length away from the two top nails:

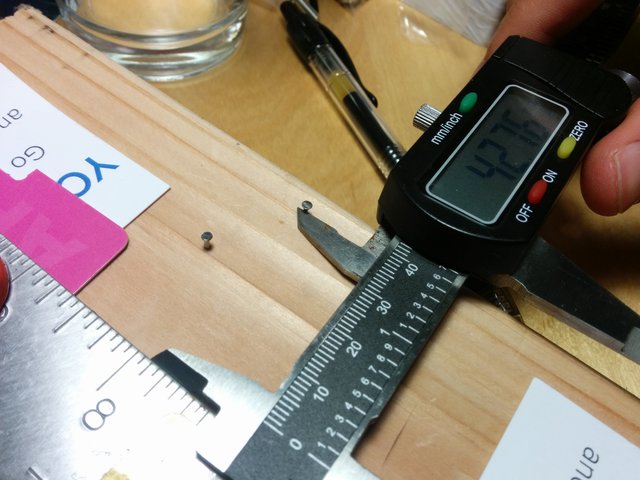
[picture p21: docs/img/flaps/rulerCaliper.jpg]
ruler alignment


Then slide a blank card under the ruler and hold it tightly against the nails while scoring along the ruler edge.

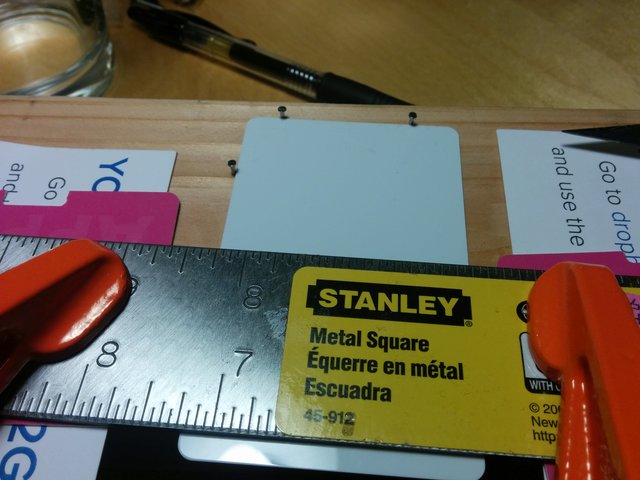
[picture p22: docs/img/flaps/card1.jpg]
card to be cut


You should get a nice clean line, which doesn't have to be too deep. 

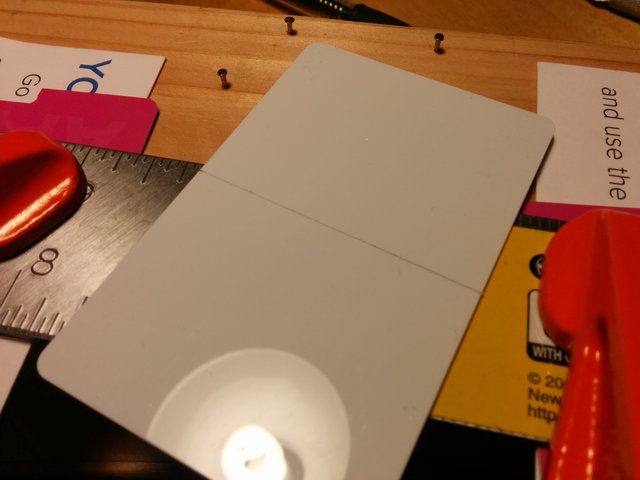
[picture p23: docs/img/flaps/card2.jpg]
card with score line


Bend the card away from the cut until it's folded back on itself, making sure that the ends of the card match up with each other (otherwise adjust the ruler alignment to correct for this). Then straighten the card and bend the opposite direction until it snaps in half.

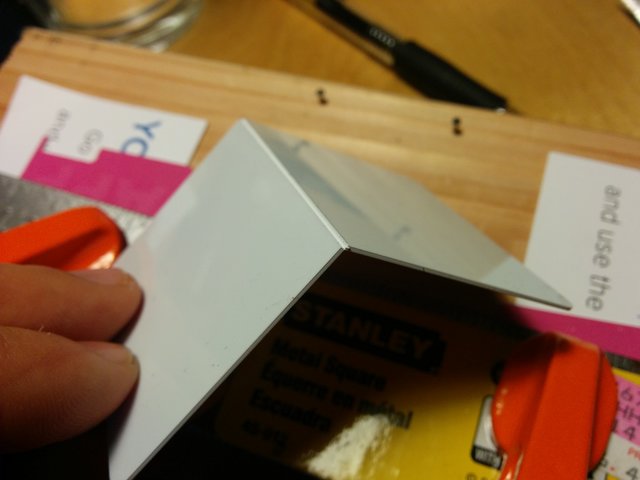
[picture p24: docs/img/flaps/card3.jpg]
folded card

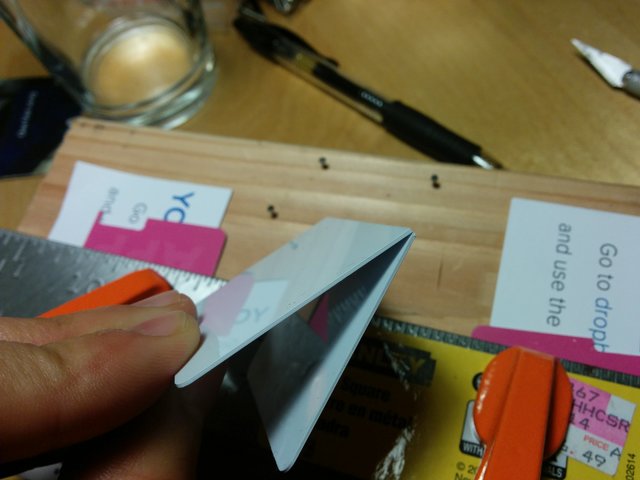
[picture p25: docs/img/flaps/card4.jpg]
folded card 2


Do this with 20 cards to get 40 half-cards. Then take each half-card and use the [[flap cutting jig|Build flap cutting jig]] to punch a notch out of each side.

punched card
stack of punched cards

 The punched holes may not be completely clean (e.g. some material left outside the hole) but that's ok. Take some diagonal cutters to clip off the excess material and clean up the top/bottom of the punched notch.

clipping card with diagonal cutters final cut flaps

If you're interested in more precise dimensions for the flaps and cutouts and the reasoning behind those values, see the discussion here: https://github.com/scottbez1/splitflap/issues/8

If you'd like to save yourself some time, an alternative to cutting your own flaps is to purchase pre-cut flaps that I've had professionally made, [available on Etsy](https://bezeklabs.etsy.com/listing/979720975). Purchasing pre-cut flaps from me will also help fund the continued development of this open-source project.

[^ Up to top](#about-flaps)

[<< Back to Documentation Index](../DocumentationIndex.md)

## 3.3 Apply letter stickers

For applying letter stickers to the flaps, I generally recommend purchasing store-bought vinyl letter sticker packs (see the [v2 complete ordering guide](/docs/v2/OrderingComplete.md) or [v0 complete ordering guide](/docs/v0/OrderingComplete.md) for details).

If you have a vinyl cutter like a Cricut or Silhouette, you can use the [generate_fonts.py](https://github.com/scottbez1/splitflap/blob/master/3d/scripts/generate_fonts.py) script to generate a custom flap letter stickers in the font/design of your choice. I recommend following [Dave Madison's excellent blog post](https://www.partsnotincluded.com/building-diy-split-flap-displays/#:~:text=Letter%20Generation) for tips on how to do this! (And kudos to Dave Madison for contributing that font generation script to the project!)

Applying the letter stickers to each of the 40 flaps is a painstaking, slow process. After a bit of practice, it still took me about 1.5 hours and a lot of patience to apply all the stickers to a new set of flaps:

video time-lapse (https://www.youtube.com/watch?v=N_ifOY9FLs8)

**Note:** I've since discovered a better way of applying letter stickers - see [New Instructions](#new-instructions). The [Old Instructions](#old-instructions) are still included below, but no longer recommended.

### New Instructions

Watch the [youtube video](https://www.youtube.com/watch?v=3lFECISLwyI):



This method is a lot less stressful and offers much better alignment than the older method.

1. Tape down old credit cards or hotel keycards so they form a U-shaped jig that cradles 2 flaps. Place 2 blank flaps into that jig. (Optionally tape another card or piece of paper that covers the bottom 3/16 inch (4.76mm) of the bottom flap -- this serves as a baseline for aligning the stickers)
1. Using food storage cling wrap applied tightly over a clear container, place the letter sticker **upside down** (sticky side UP) on the cling wrap. It should be attracted to the cling wrap because of static electricity, which will allow us to flip the whole thing over without the sticker falling off.
1. Flip the container+cling wrap+sticker over, and looking through the clear container and cling wrap, align the letter onto the 2 flaps (using the optional baseline alignment guide mentioned above, if you have it). Press the container down so the sticker adheres to the flaps and remove the container.
1. Using your finger, press down all over the letter sticker to ensure it's adhered and there are no air bubbles.
1. Cut the letter sticker in half along the gap between the 2 flaps.
1. Remove the bottom flap from the jig and set aside. Take the top flap and flip down so it's in the place of the bottom flap, and place a new blank flap in the top position.
1. Repeat steps 2-6 with the next letter sticker.

### Old Instructions

I've found it's easiest to keep the order correct by starting with all but two of the (empty) flaps already on the spool. You can add/remove flaps on the spool by gently squeezing the flap so the middle of the flap bows away from the spool's center: hold your index finger in a cup shape underneath the flap so only the flap's edges touch your finger, and then press your thumb into the center so the flap bends to follow the contour of your index finger. This will cause the pins to move inward enough to slide the flap into or out of place:

Gently bend the flap to add/remove it from the spool

Start with just 2 empty flaps off the spool, flat on your workspace arranged as they would be on the spool (vertically mirroring each other, with the pins in the middle).

For each letter:

1. Use a hobby knife to cut the letter sticker in half. I used a spare PVC card cut to 1.5 inches tall as a guide since it's smaller and easier to move around than a ruler.
1. Peel up half the letter (you can use the knife's blade to help separate the sticker from the backing), and carefully apply it to one of the flaps, with the cut edge along the flap's cut edge.
1. Repeat with the other half of the letter, making sure to align it with the half you already placed.
1. Take the bottom flap and place it back on the spool, in the lower of the two available slots.
1. Take the top flap (still sitting on your workspace) and flip it vertically so it's face-down in the bottom-flap orientation.
1. From the spool, remove the empty flap above the empty slot (above ), and place it on your workspace in the top-flap orientation.
1. Repeat the steps for each letter. You will always be placing the bottom half of the next letter on the back of the flap that has the top half of the previous letter (e.g. the bottom half of "C" is on the back of the flap with the top half of "B", and the bottom half of "9" is on the same physical flap as the top half of "8").

[^ Up to top](#about-flaps)

[<< Back to Documentation Index](../DocumentationIndex.md)

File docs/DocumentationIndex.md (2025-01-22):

# Splitflap Documentation Index
This is the documentation for the open-source splitflap display project: https://github.com/scottbez1/splitflap

Questions or comments? Join the [community Discord server](https://discord.gg/wgehm3PcrC) to chat with other split-flap enthusiasts.

# General
* [Flaps Guide](Flaps.md) - overview of the flaps - the most repetitive (and sometimes tedious) part of this project: How to cut them yourself or purchase them pre-cut and pre-printed
* [28BYJ-48 Motor Buying Guide](MotorGuide.md) — motor buying guide (finding good motors is a little tricky, so it has its own guide)
* [Electronics User Guide](ElectronicsGuide.md)  — Chainlink electronics setup guide

# v2
## Ordering
* [v2 Easy Ordering Guide (US only)](v2/OrderingEasy.md)  — simplified ordering overview if you’re in the US
* [v2 Comprehensive/Advanced Ordering Guide](v2/OrderingComplete.md)  — the FULL exhaustive ordering document, with lots of alternatives and options for every part

## Assembly
* [v2 Assembly](v2/Assembly.md)  — assembly overview for the newer v2 mechanical release

# v0
## Ordering
* [v0 Easy Ordering Guide (US only)](v0/OrderingEasy.md)  — simplified ordering overview if you’re in the US
* [v0 Comprehensive/Advanced Ordering Guide](v0/OrderingComplete.md)  — the FULL exhaustive ordering document, with lots of alternatives and options for every part

## Assembly
* [v0 Assembly](v0/Assembly.md)  — mechanical assembly overview for the stable 0.5/0.6/0.7 versions

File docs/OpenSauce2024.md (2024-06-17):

Split flap display at Open Sauce

# What's a split-flap display?
A [split-flap](https://en.wikipedia.org/wiki/Split-flap_display) is an electro-mechanical display technology, previously common in airports and train stations, and named for the letter flaps that are split in half.

Split-flap displays have a few advantages compared to modern LED/LCD displays, like:
- 🔋 no power required when contents are static
- 💡 no glow like a light-based display
- 🔊 makes sound when new information is available (like when your flight is canceled!)
- 😎 sounds and looks sweet

But they have one BIG disadvantage: **maintenance/complexity** 🙀



# How does it work?
Check out this video for a basic overview:

<a href="https://www.youtube.com/watch?v=UAQJJAQSg_g" target="_blank">
  
</a>

# How do I build one?
Check out the [github repo](https://github.com/scottbez1/splitflap) to find source designs as well as links to instructions and ordering info.

I also sell some of the custom parts in my [Etsy store](https://bezeklabs.etsy.com) for your convenience (and to help fund continued development), but it's all open source so you're always welcome to build everything yourself!

<a href="https://bezeklabs.etsy.com" target="_blank">
  
</a>

The [splitflap community Discord server](https://discord.com/invite/wgehm3PcrC) is the best place to keep up with the latest changes or ask questions about the project!

# Why????
I love old mechanical technology, and I'm always a little sad when beautiful mechanical solutions are replaced by (far more practical) big, bright, colorful LEDs, so I sought to recreate split-flaps with more modern hobbyist-friendly tools.

It's become a passion project of mine over the last 9 years, and I LOVE seeing the displays and art installations others have built based on this open-source design!

# Contact/chat info
 - Splitflap project Discord server: https://discord.gg/Hxnftc8PyW - best place to ask general questions or see what's happening on the project
 - Email: scott@bezeklabs.com
 - YouTube: [@scottbez1](https://youtube.com/scottbez1)
 - Twitter: [@scottbez1](https://twitter.com/scottbez1)
 - Mastodon: [@scottbez1@fosstodon.org](https://fosstodon.org/@scottbez1)

# Acknowledgements
 - A huge thank you to:
   - Ben Flatau for being the mastermind behind the giant display and for all his time and help with Open Sauce 2023 and 2024
   - the City of Palo Alto whose art grant for [Code:ART 2021](https://www.cityofpaloalto.org/Departments/Community-Services/Arts-Sciences/Public-Art-Program/CodeART/CodeART-2021) originally made it possible to build something this big
   - and the whole team of volunteers that helped assemble/paint/install the 4320 flaps, electronics, and structure
 - Much of the original design inspiration came from some blog posts by The Beach Lab, which sadly don't seem to be online anymore and I haven't been able to find archives, but IIRC this is where the CR80 card idea and laser-cut drum structure came from
 - [Dave Madison built and documented](https://www.partsnotincluded.com/building-diy-split-flap-displays/) some great improvements on this design, and has contributed a ton of those changes back to the project, including the font generation script for custom vinyl cut or printed flaps!
 - And thank you to [everyone else who has contributed to the project over the years!](https://github.com/scottbez1/splitflap/graphs/contributors)

# Other notable split-flap displays
 - [Oat Foundry](https://www.oatfoundry.com/split-flap/) makes custom commercial displays
 - [Vestaboard](https://www.vestaboard.com/) makes a compact version for home/office use
 - [Engineezy](https://www.youtube.com/watch?v=K_UEkRFP7fs) designed a 3d-printed version as a scoreboard
 - And lots of other DIY / Open Source designs!

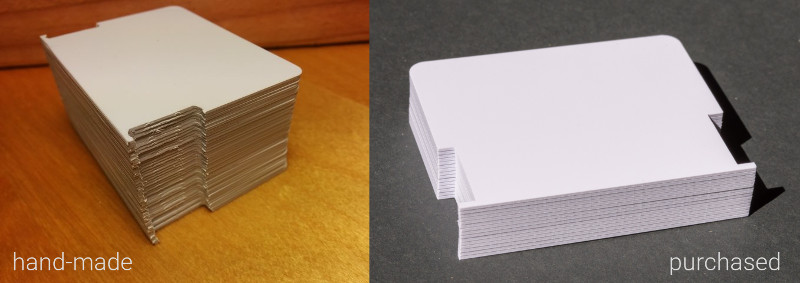
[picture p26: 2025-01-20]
docs/img/flaps/flapQuality.jpg

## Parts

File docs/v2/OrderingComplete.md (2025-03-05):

# Splitflap v2 Comprehensive Ordering Guide
[<< Back to Documentation Index](../DocumentationIndex.md)

The instructions below will walk you through ordering all the parts (excluding common tools) needed to build a splitflap v2 display with **6 modules** using the latest Chainlink electronics.

Ready to assemble? Jump ahead to the [Assembly Guide](Assembly.md) 

If you have any questions, please feel free to reach out to me (scott@bezeklabs.com). Or, join the [Discord server](https://discord.gg/wgehm3PcrC), to discuss or ask questions from the wider split-flap community!

😩 Feeling overwhelmed by this document? I don’t blame you, there’s a LOT here… So I put together a much shorter document that favors simplicity over comprehensiveness/lowest-cost,
for people in the US: [+Splitflap Ordering (the “easy” route)](OrderingEasy.md) 

1. [Order laser-cut parts](#order-laser-cut-parts)
3. [Order electronics](#order-electronics)
2. [Order hardware](#order-misc-hardware)

----------
# Order laser-cut parts

There are many places you can get laser-cut parts, but I’ve personally used Ponoko and Elecrow for ordering shipped to the US with an easy online-only process. I’ve previously recommended ordering from Ponoko - and while I still believe they have great quality and customer service so you'll get a great product, they’ve gotten too expensive to be my default recommendation any longer 😞 

For advanced makers: if you want to cut a single front panel that will be shared by an entire row (or grid) of modules, there is a script to do so with lots of configurable options like spacing, rows/cols, and even has a mode for generating geometry for CNC routing with necessary “dog-bones” applied to inside corners — see `generate_combined_front_panel.py`

💡 Note: v2 laser-cut parts are not dimensionally compatible with older v0 modules! If you’re extending an older display, make sure to use the older files (see the v0 [ordering instruction](../v0/OrderingComplete.md))

## Elecrow (recommended)

- Download the appropriate file:
  - 52-flap design
    - 3mm acrylic
      - Download [zip](https://s3.amazonaws.com/splitflap-artifacts/refs/tags/releases/mechanics/v2/3d/3d_laser_vector-52-elecrow-3mm-acrylic_1x.zip)
      - Go to [Elecrow acrylic laser cutting](https://www.elecrow.com/acrylic-cutting.html) and upload the zip file
      - Enter dimensions: 
      - Select thickness: 3mm
      - Engrave: No
      - Acrylic color: Matte Black (P502) is recommended
    - 3mm wood
      - Download [zip](https://s3.amazonaws.com/splitflap-artifacts/refs/tags/releases/mechanics/v2/3d/3d_laser_vector-52-elecrow-3mm-wood_1x.zip)
      - Go to [Elecrow wood laser cutting](https://www.elecrow.com/5pcs-wood-laser-cutting-service.html)
      - Dimension: 20cm Max * 20cm Max(Thickness: 3mm)
  - 40-flap design
    - 3mm acrylic
      - Download [zip](https://s3.amazonaws.com/splitflap-artifacts/refs/tags/releases/mechanics/v2/3d/3d_laser_vector-40-elecrow-3mm-acrylic_1x.zip)
      - Go to [Elecrow acrylic laser cutting](https://www.elecrow.com/acrylic-cutting.html) and upload the zip file
      - Enter dimensions: 
      - Select thickness: 3mm
      - Engrave: No
      - Acrylic color: Matte Black (P502) is recommended
    - 3mm wood
      - Download [zip](https://s3.amazonaws.com/splitflap-artifacts/refs/tags/releases/mechanics/v2/3d/3d_laser_vector-40-elecrow-3mm-wood_1x.zip)
      - Go to [Elecrow wood laser cutting](https://www.elecrow.com/5pcs-wood-laser-cutting-service.html)
      - Dimension: 20cm Max * 20cm Max(Thickness: 3mm)

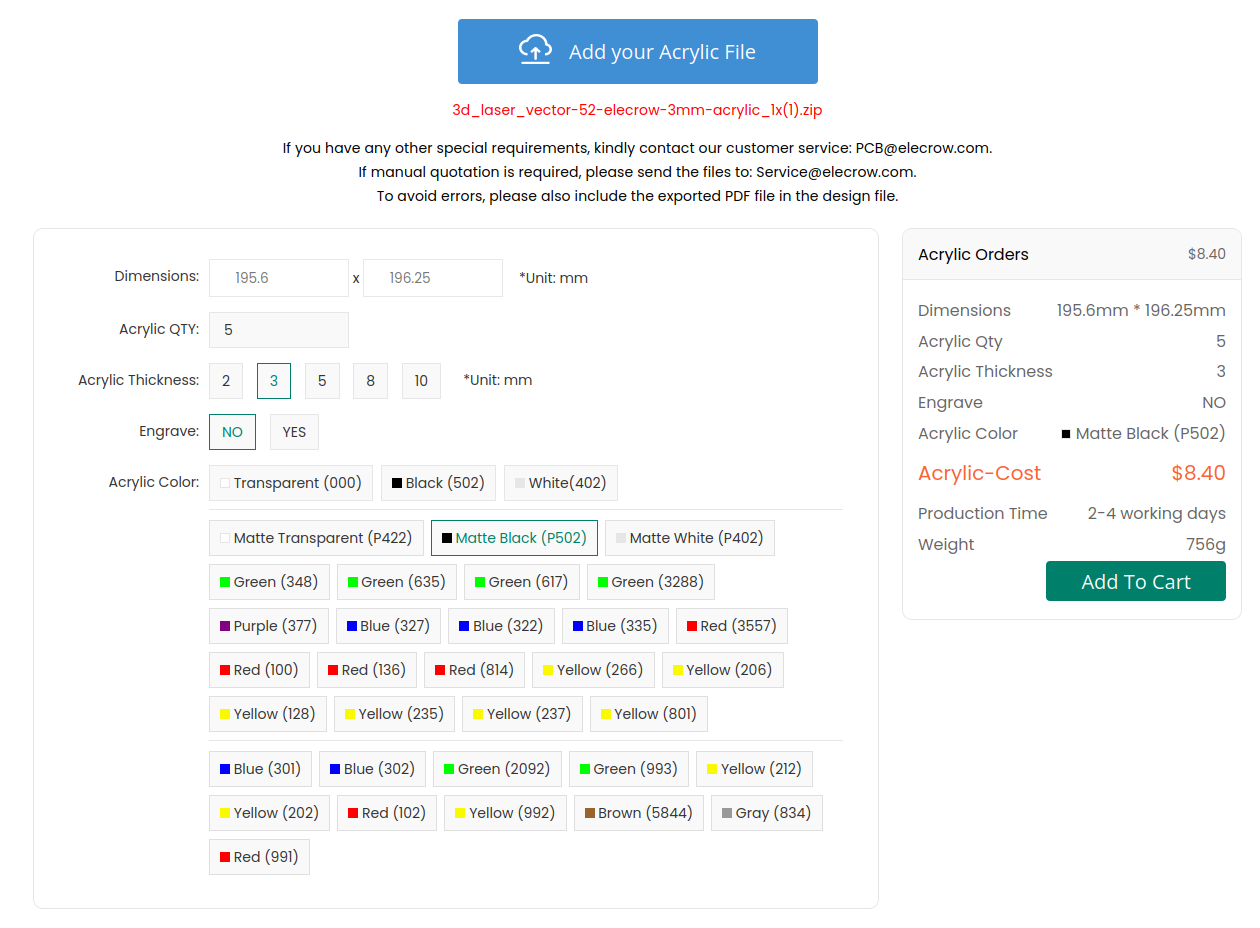
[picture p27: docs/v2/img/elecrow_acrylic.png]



## Ponoko (also recommended, but pricey)
- Download the appropriate file
    - 52-flap design
        - 3mm Acrylic: [svg](https://s3.amazonaws.com/splitflap-artifacts/refs/tags/releases/mechanics/v2/3d/3d_laser_vector-52-ponoko-3mm-acrylic_1x.svg) 
        - 3mm MDF: [svg](https://s3.amazonaws.com/splitflap-artifacts/refs/tags/releases/mechanics/v2/3d/3d_laser_vector-52-ponoko-3mm-mdf_1x.svg) 
    - 40-flap design
        - 3mm Acrylic: [svg](https://s3.amazonaws.com/splitflap-artifacts/refs/tags/releases/mechanics/v2/3d/3d_laser_vector-40-ponoko-3mm-acrylic_1x.svg) 
        - 3mm MDF: [svg](https://s3.amazonaws.com/splitflap-artifacts/refs/tags/releases/mechanics/v2/3d/3d_laser_vector-40-ponoko-3mm-mdf_1x.svg) 

- Go to [Ponoko](https://www.ponoko.com/) and sign up for an account.
- [Upload](https://www.ponoko.com/designs) the SVG file from above. Confirm the dimensions match the values above, and check that blue lines are set for “Cutting” and black fill is set for “Area Engraving” (or turn this off to skip engraved features)


- Select a material - [MDF](https://www.ponoko.com/materials/mdf-fiberboard) or [Acrylic](https://www.ponoko.com/materials/black-matte-acrylic) are recommended — choose 3.0mm (0.12 inches) thickness. Make sure to check the material’s maximum size against the dimensions provided next to the file links above; some materials may be too small to order the 4x versions.

💡 **Important note if ordering Matte 1-Side acrylic at Ponoko:** you ***must*** immediately send special instructions to Ponoko after placing your order, requesting to have the design engraved on the *glossy* side. This will result in the design being correctly cut so the matte surface will be on the exterior of the display when assembled. From Ponoko support (as of 2021-05-13): 

> The matte is [by default] cut with the matte side up (so engraving happens on this side as well).
> 
> If you would like to place an order and have us engrave on the glossy side, just **reply to the order confirmation page** with your request and we'll be sure to make note in the order details.

----------
# Order electronics

The Chainlink system is a newer electronics system based around the more powerful ESP32 microcontroller (which adds things like wifi support) and incorporates learnings from the earlier Classic Controller. New development is focused on the Chainlink system.

The basic pieces that you’ll need for a Chainlink system:

- **Chainlink Driver board** (1 for every 6 split-flap modules you want to control)
- **Chainlink Buddy** + **ESP32** (1 for the whole display, regardless of size)
- **Sensors** (1 for every split-flap module)

The easiest and best-supported approach is to purchase each of those items from the Bezek Labs Etsy store (US only) - I’ve set up the store so that items comes with the necessary accessories, meaning there are fewer things you need to track down and purchase separately from different suppliers. Proceeds also help fund continued development of the project!

💡 See the [Chainlink User Guide](../ElectronicsGuide.md) for more info about different configurations.

## Order Chainlink Driver


The Chainlink Driver is what drives up to 6 split-flap modules. Multiple Chainlink Drivers can be chained (hence the name!) to create much larger displays (I have created a 108-module display using 18 Chainlink Driver boards).

The Chainlink Driver uses mostly surface-mount components so it’s optimized for factory production moreso than hand-soldering (though you can of course do that if you’d like)

[**Recommended] Option 1: Purchase fully-tested PCBA on Etsy (US shipping only)**
I sell mostly-pre-assembled [Chainlink Driver boards in the Bezek Labs Etsy store](https://bezeklabs.etsy.com/listing/1123280069/splitflap-chainlink-driver-v11) (includes accessories: connectors, ribbon cable)

These have all the tricky surface-mount components already soldered for you. You’ll just need to solder the through-hole connectors, which are pretty easy.

Every single board that I sell goes through a rigorous 100% functionality test which validates every single motor output, sensor input, LED, and data line works as expected, using a custom test jig I developed.

This option also includes all the connectors and ribbon cable you’ll need, so you don’t need to order anything separately!

And, if you want to make sure you get the right 28byj-48 motors instead of just ordering on AliExpress and hoping for the best, I’ve added an option on Etsy to include 6x motors with your Chainlink Driver order! Yes, they’re more expensive than ordering on AliExpress directly, but they’ll ship quickly and you’ll know you’re getting good motors.

**Option 2: Purchase assembled Chainlink Driver from JLCPCB, and purchase connectors and ribbon cable separately**
The Chainlink Driver design is optimized for JLCPCB assembly, so it’s mostly a drag-and-drop process, but you’ll need to carefully understand the options you select. Most importantly, if JLCPCB is out of stock of a component, *they will continue to build your order and simply omit that component!* So be careful to check all warnings or notices that appear when ordering.

Note that JLCPCB assembly involves a number of fixed costs (such as $3 per unique part, and shipping fees) which make larger quantities a better value. 

Download the following 3 items from the latest Chainlink Driver release (v1.1):

- gerber files (for the PCB)
- BOM (specifies which components are needed for assembly)
- CPL (specifies placement locations for components)

To order:



- Go to JLCPCB https://cart.jlcpcb.com/quote
- Upload gerber zip
- Select your quantity, PCB color
- Confirm other parameters:
    - Dimensions: (accept auto-generated dimensions, which will likely be 30.48 x 198.12)
    - PCB Thickness: 1.6
    - Outer Copper Weight: 1oz



- Select SMT Assembly
    - Assemble top side
    - Select your quantity to assemble
    - Tooling holes: select **Added by Customer** (these are included in the design already, so you do not need JLC to add them)
    - Confirm



- Upload BOM File
- Upload CPL (csv) file



- Review parts
    - ⚠️ Make sure you check this step carefully, as any parts that are out of stock will simply be omitted! ⚠️ 
    - “No part selected” is *normal* for several connectors that will not be assembled by JLCPCB (see below) - these will be “J”-prefixed designators such as “Motor A”, “Sensor C”, or “Input” or “Output”

- Review parts placement
- Save to Cart
- Checkout (note that JLC does NOT reserve parts until you’ve checked out and paid your order, so if stock is low there is a chance parts will be missing if you wait to pay!)

If you wish to hand-assemble some of the through-hole connectors rather than having JLCPCB assemble them for you, you can unselect these components when placing your order, then order and assemble them yourself:

- 2x IDC shrouded connectors, 2x4, 2.54mm spacing, e.g. JLC/LCSC [C601937](https://lcsc.com/product-detail/IDC-Connectors_JILN-321008SG0ABK00A01_C601937.html), or on [Digi-Key](https://www.digikey.com/en/products/detail/adam-tech/BHR-08-VUA/9832409)
- 6x JST XH 5 pin connectors, e.g JLC/LCSC [C161872](https://lcsc.com/product-detail/Wire-To-Board-Wire-To-Wire-Connector_JST-Sales-America-B5B-XH-AM-LF-SN_C161872.html). or [C378947](https://lcsc.com/product-detail/Wire-To-Board-Wire-To-Wire-Connector_JST-Sales-America-B5B-XH-A-BK-LF-SN_C378947.html), or LCSC [C157991](https://lcsc.com/product-detail/Wire-To-Board-Wire-To-Wire-Connector_JST-Sales-America-B5B-XH-A-LF-SN_C157991.html), or on [Digi-Key](https://www.digikey.com/en/products/detail/jst-sales-america-inc/B5B-XH-AM-LF-SN/1651037)
- 6x 3-pin male headers, 2.54mm spacing, e.g. JLC/LCSC [C49257](http://), or on Digi-Key [3-pin](https://www.digikey.com/en/products/detail/sullins-connector-solutions/PREC003SAAN-RC/2774851) or purchase [40-pin](https://www.digikey.com/en/products/detail/sullins-connector-solutions/PREC040SAAN-RC/2774814) and break apart, (or readily available in bulk on Amazon, etc)

In order to connect your Chainlink Driver to your microcontroller (or to another Chainlink Driver in a chain), you’ll also need an IDC ribbon cable + connectors:

- 1x 8 conductor 1.27mm spacing ribbon cable (45cm recommended minimum length for chaining), [e.g. on Digi-Key](https://www.digikey.com/en/products/detail/w%C3%BCrth-elektronik/63910815521CAB/8324550)
- 2x IDC cable connectors, e.g. LCSC [C601910](https://lcsc.com/product-detail/IDC-Connectors_JILN-531408YBS0BW01_C601910.html), or on [Digi-Key](https://www.digikey.com/en/products/detail/adam-tech/FCS-08-SG/9832361)
- You could alternatively look for an assembled 8P IDC cable on e.g. Amazon, though make sure it's a straight-through cable (i.e. notches on the connectors both face the same way)

You may get an email from JLCPCB after placing your order, asking to double-check the orientation of the screw terminals. See images below for the correct orientation: the wires would go *over* the Power labels on the PCB to be inserted into the front of the screw terminals.

✅ 3d model of the design with CORRECT screw terminal orientation
✅ Confirmation email from JLCPCB, showing CORRECT screw terminal orientation. If the image they send you looks like this, go ahead and confirm it!
🚫 INCORRECT: If it looks like this, it’s facing the WRONG way!

**Option 3: Purchase bare PCB, components, and hand-assemble**
This is an advanced option which will require hand-soldering surface mount components. While the components aren’t tiny (ICs are SOIC packages and passives are 0603), it will require some skill and patience.

You might also consider ordering a stencil and reflow soldering the components yourself. However, be aware that the PCB is long and thin so it is prone to warping when heated, so you may have difficulty if you plan to use a hot plate rather than an oven.

Follow the instructions from Option 2 above for ordering the PCBs, and instead of selecting assembly, you can use the BOM file to order all the components yourself. The BOM file uses LCSC part numbers.

## Order Chainlink Buddy and ESP32

You’ll connect your ESP32 microcontroller to the first Chainlink Driver in the chain. The best way to do this is with one of the available Chainlink “Buddy” boards, which allow you to plug in the IDC/ribbon cable directly. 

Many different ESP32 modules exist, and most of them should be compatible (as long as they are dual-core), but I strongly recommend the TTGO T-Display (on [Amazon](https://amzn.to/3kHwhMm) for quick shipping [affiliate links help support this project at no cost to you, or use a [non-affiliate link](https://www.amazon.com/LILYGO-T-Display-Arduino-Development-CH9102F/dp/B099MPFJ9M) if you’d prefer], or [AliExpress](http://) if you don’t mind waiting). It includes a 240x135 LCD that the splitflap firmware supports out of the box, which can be very useful for debugging.

**Chainlink Buddy [T-Display]**



The Chainlink Buddy [T-Display] is the recommended approach for most people, and makes it really easy to connect a TTGO T-Display microcontroller to your Chainlink system, with a ribbon cable connector, screw terminals for power, and a barrel jack for convenient 12v power input.

[Recommended] Available [in the Bezek Labs Etsy store (US only)](https://bezeklabs.etsy.com/listing/1109357786/splitflap-chainlink-buddy-t-display) (includes accessories: IDC connector, screw terminals, barrel jack, and female headers).
There’s also an option to include the T-Display ESP32 module as well if you want to make sure you get the right thing.

or, you can order the PCB yourself using the gerbers, and you will also need to order the following items to go with it:

- 1x IDC shrouded connectors, 2x4, 2.54mm spacing, e.g. LCSC [C601937](https://lcsc.com/product-detail/IDC-Connectors_JILN-321008SG0ABK00A01_C601937.html)
- 1x 3-pin 5.08mm spacing screw terminal, e.g. LCSC [C72334](https://lcsc.com/product-detail/Screw-terminal_Ningbo-Kangnex-Elec-WJ500V-5-08-3P_C72334.html)
- 1x 2.1mm barrel jack, e.g. LCSC [C381116](https://lcsc.com/product-detail/AC-DC-Power-Connectors_XKB-Connectivity-DC-005-5A-2-0_C381116.html)
- 2x 12-pin 2.54mm spacing female headers, e.g. LCSC [C350303](https://lcsc.com/product-detail/Female-Headers_HOAUC-2685Y-112CNG1SNA01_C350303.html)

**Chainlink Buddy [Breadboard] (alternative to the T-Display Buddy)**



If you’d like to use a different ESP32 module than the T-Display, the Breadboard Buddy is an alternative to the  simple way to cleanly connect the Chainlink ribbon cable to a breadboard for prototyping. This is not generally recommended, but is available for advanced users.

Available [in the Bezek Labs Etsy Store (US only)](https://bezeklabs.etsy.com/listing/1123863267/splitflap-chainlink-buddy-breadboard) (includes accessories: IDC connector, male pin headers)

or, you can order the PCB yourself using the gerbers and you will also need to order the following items to go with it:

- 1x IDC shrouded connectors, 2x4, 2.54mm spacing, e.g. LCSC [C601937](https://lcsc.com/product-detail/IDC-Connectors_JILN-321008SG0ABK00A01_C601937.html)
- 1x 5-pin 2.54mm spacing male pin headers

## Order Sensors

Each split-flap module will need a hall effect sensor to detect the home position. The best way to mount this is with a small sensor PCB.

[**Recommended] Option 1: Sensor kit v2 on Etsy (US only)**
To keep things simple, this kit includes 6 sets of all the parts you’ll need to assemble sensors:

- 6x Sensor PCB
- 6x 3-pin right angle headers
- 6x 4mm magnet (this will mount onto your spool)
- (optional) 6x sensor cables

https://bezeklabs.etsy.com/listing/1696745674

**Option 2: Order partially-assembled PCBs directly, and order other parts separately**
The v2 sensor design is optimized for JLCPCB assembly, so it’s mostly a drag-and-drop process, but you’ll need to carefully understand the options you select. Most importantly, if JLCPCB is out of stock of a component, *they will continue to build your order and simply omit that component!* So be careful to check all warnings or notices that appear when ordering.

Note that JLCPCB assembly involves a number of fixed costs (such as $3 per unique part, and shipping fees) which make larger quantities a better value.

The sensor PCBs are simple enough that you can easily hand-solder them, so I'd actually recommend Option 3 below (ordering bare PCBs and parts and assembling them yourself) unless you are building a larger display.

To order assembled sensor v2 PCBs, download the following 3 items from the latest v2 sensor release:

- [Panelized gerber files](https://s3.amazonaws.com/splitflap-artifacts/refs/tags/releases/sensor-smd/v2/electronics-v2/sensor_smd-panelized-jlc/gerbers.zip) (for the PCB)
- [Panelized BOM](https://s3.amazonaws.com/splitflap-artifacts/refs/tags/releases/sensor-smd/v2/electronics-v2/sensor_smd-panelized-jlc/bom.csv) (specifies which components are needed for assembly)
- [Panelized CPL](https://s3.amazonaws.com/splitflap-artifacts/refs/tags/releases/sensor-smd/v2/electronics-v2/sensor_smd-panelized-jlc/pos.csv) (specifies placement locations for components)

To order:

- Go to JLCPCB https://cart.jlcpcb.com/quote
- Upload gerber zip
  - Set parameters:
      - Layers: 2
      - Dimensions: (accept auto-generated dimensions)
      - PCB Qty: 5 (remember, the "panel" that you're ordering includes 6x sensors per panel, so the total sensors will be 6x the PCB Quantity you enter here! i.e. you will end up with 30 sensor PCBs with an order of 5 PCBs. You can have fewer than this quantity assembled)
      - Product Type: Industrial/Consumer electronics
  - PCB specifications
      - Different design: 1
      - Delivery format: Panel by Customer
      - Panel Format:
          - Column: 2
          - Row: 3
      - PCB Thickness: 0.8mm ⚠️ This is not the default PCB thickness - make sure to select 0.8mm!
      - PCB Color: green is cheapest considering the less-common 0.8mm thickness
      - LeadFree HASL
  - Other options - leave all of these as defaults<br>

- Select PCB Assembly
    - Note: JLCPCB gives you the choice to only assemble a portion of PCBs you've ordered. In this example, I've shown ordering 5 PCBs (the minimum quantity) and only having 2 of the 5 assembled (the minimum assembly quantity).
    - Assemble top side
    - PCBA Type: Economic
    - PCBA Qty: 2 (This is 2 of the 6x _panels_, for 12x total sensor PCBs. If this option doesn't appear, change PCBA type to Standard then back to Economic!)
    - Tooling holes: Added by JLCPCB
    - Confirm Parts Placement: No (select Yes if you'd like extra assurance and know how to review the production gerber files they provide)
    - Parts Selection: By Customer
    - Advanced Options: leave these all as defaults<br>

- Upload BOM File
- Upload CPL (csv) file
- Make sure to select File provided as: "Complete File, just proceed with my own files"
  Screenshot from 2025-03-04 22-32-38

- Review parts
    - ⚠️ Make sure you check this step carefully, as any parts that are out of stock will simply be omitted! ⚠️
  Screenshot from 2025-03-04 22-33-01

- Review parts placement
  Screenshot from 2025-01-19 23-50-15

- Save to Cart
- Checkout (note that JLC does NOT reserve parts until you’ve checked out and paid your order, so if stock is low there is a chance parts will be missing if you wait to pay!)

You'll also need to purchase these items separately:
- 6x 4mm round magnet (e.g. [Digi-Key](https://www.digikey.com/en/products/detail/radial-magnets-inc/9027/5218822))
- 6x 3-pin right-angle pin headers (e.g. [Digi-Key](https://www.digikey.com/en/products/detail/sullins-connector-solutions/PREC003SBAN-M71RC/2774931))
- 6x 300mm 3-pin “servo” male-to-male cable (e.g. [Amazon](https://amzn.to/3FdxP8K) (10 pack) [or, [non-affiliate link](https://www.amazon.com/VIMVIP-10pcs-300mm-Extension-Futaba/dp/B00N8OX7VO)], or [AliExpress](https://www.aliexpress.com/item/32800106648.html) (10 pack))
https://bezeklabs.etsy.com/listing/966380990/splitflap-sensor-pcb-set-bare

**Option 3: Order bare PCBs directly, and order all parts separately**
Follow the instructions above to order the PCBs but skip the assembly portion.

In addition to the parts mentioned above (magnets, connectors, cables) you’ll also need to order the parts for the PCB itself:
- 6x hall effect sensors (e.g. HX6286, LCSC [C495736](https://www.lcsc.com/product-detail/Hall-Switches_HUAXIN-HX6286ESO_C495736.html?s_z=n_C495736))
- (optional) 6x 0603 red LED (e.g. LCSC [C2286](https://www.lcsc.com/product-detail/LED-Indication-Discrete_Hubei-KENTO-Elec-KT-0603R_C2286.html?s_z=n_C2286))
- (optional for LEDs) 6x 0603 1k resistor (e.g. LCSC [C21190](https://www.lcsc.com/product-detail/Chip-Resistor-Surface-Mount_UNI-ROYAL-Uniroyal-Elec-0603WAF1001T5E_C21190.html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))
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

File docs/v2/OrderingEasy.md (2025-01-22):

# Splitflap v2 Ordering guide
[<< Back to Documentation Index](../DocumentationIndex.md)

This is the “easy” way to order the parts for your splitflap display (United States only). It optimizes for *simplicity in ordering*, not the *lowest possible cost*.

If you’d like to review other options, which could be somewhat cheaper, check out the [full ordering doc](OrderingComplete.md), but if that’s a little overwhelming, you’re in the right place here!

If you have questions, please ask in the [community Discord server](https://discord.gg/Hxnftc8PyW)!

## Laser-cut mechanical parts

**Supplier:** [Elecrow](https://www.elecrow.com/acrylic-cutting.html) has reasonable quality at a decent price

**Material:** Acrylic

The v2 design officially supports either 52 flaps per module or 40 flaps per module. The 52-flap design is the default recommendation here and is perfect if you will be buying the pre-printed "Epilogue" flap sets, but you can check out the advanced ordering instructions for details on the 40 flap variant.

For reference, the front face of each module is approximately **82.6mm wide** and **143.53mm tall**.

- [ ] Use this file to order a 52-flap design, made of 3mm acrylic (Matte Black (P502) is recommended): [zip](https://s3.amazonaws.com/splitflap-artifacts/refs/tags/releases/mechanics/v2/3d/3d_laser_vector-52-elecrow-3mm-acrylic_1x.zip)
    - Go to [Elecrow acrylic laser cutting](https://www.elecrow.com/acrylic-cutting.html) and upload the zip file
    - Enter dimensions: 
    - Select thickness: 3mm
    - Engrave: No
    - Acrylic color: Matte Black (P502) is recommended

Full ordering instructions, and alternative files for acrylic/mdf or for 40- rather than 52-flap modules can be found [here](OrderingComplete.md).

I’ve previously recommended ordering from Ponoko - and while I still believe they have great quality and customer service, they’ve gotten too expensive to be my default recommendation any longer 😞 

## Electronics

**Supplier:** [Bezek Labs](https://bezeklabs.etsy.com) (yes, I’m biased in recommending my own store, but it really is the easiest purchasing option since these are custom boards and I also include all necessary accessories). 

- [ ] [Chainlink Driver](https://bezeklabs.etsy.com/listing/1123280069/splitflap-chainlink-driver-v11) (1 for every 6 character modules)
    - Ribbon cable length: **45cm**
    - Add motors? **Yes, add 6x 28BYJ-48**
- [ ] [Sensor kit v2 (6x with magnets and headers)](https://bezeklabs.etsy.com/listing/1696745674/splitflap-sensor-kit-v2-beta-6x-with)  (1 for every 6 character modules)
    - Include cables? **YES**
- [ ] [Chainlink Buddy [T-Display]](https://bezeklabs.etsy.com/listing/1109357786/splitflap-chainlink-buddy-t-display) (1 for your *entire* display, up to 36 total character modules)
    - Include ESP32 T-Display Module: **YES**

## Flaps

**Supplier:** [Bezek Labs](https://bezeklabs.etsy.com) (again, I’m biased, but there aren’t any commercial alternatives and making them yourself requires a lot of [time and patience](../Flaps.md#option-3-diy-flaps))

**Two good options** (this tradeoff is totally up to you):

- [ ] [”Epilogue” pre-printed v2 flaps](https://bezeklabs.etsy.com/listing/1685633114/splitflap-epilogue-printed-flaps-beta-52) save a TON of time and look great, but are definitely more expensive. 6-packs and 24-packs are available at a small discount. Only available with white text on a black card.

OR

- [ ] You can buy blank flaps and [apply letter stickers to them yourself](https://www.youtube.com/watch?v=3lFECISLwyI)
    - [ ] [blank flaps](https://bezeklabs.etsy.com/listing/979720975/blank-splitflap-display-flaps) (purchase the 1x52 or 6x52 packs for a 52-flap design. The 6x packs are available at a small discount)
    - [ ] [vinyl letter stickers](https://amzn.to/37Frsjb) (from Amazon). Blank flaps are available in white or black, and vinyl letter stickers are [available](https://amzn.to/3ieAZj9) in [many](https://amzn.to/37t1y1R) different [colors](https://amzn.to/3tk4Ddh). (1 sticker pack for every **2** modules)

## Hardware

**Supplier:** McMaster-Carr (reliable, but somewhat pricey especially with shipping) or find these common items elsewhere

- [ ] M4 x 10mm **button-head**. 10 bolts needed per module (so you’ll need at least 60x for 6 modules). Must be button-head style (e.g. taller socket-cap bolts will likely cause clearance issues)
    - [McMaster-Carr](https://www.mcmaster.com/92095A190/) pack of 100
- [ ] M4 hex nuts. 10 nuts needed per module (so you’ll need at least 60x for 6 modules)
    - [McMaster-Carr](https://www.mcmaster.com/91828A231/) pack of 100

## Power supply and wiring

**Supplier:** many options, no specific recommendations

For 1-12 modules:

- [ ] 22AWG wire for 3.3v power (gauge is not critical as this is low-current; solid wire is preferable to stranded for use with screw terminals)
- [ ] 12V power supply capable of *at least* **1.5A for every 6 modules**, plus some margin. Searching for “12V CCTV” or LED power supplies is a good way to find supplies that will have the correct barrel jack connector to plug into the Chainlink Buddy [T-Display]. 
    - Assume that the current ratings on supplies sold by Amazon, AliExpress, etc are overstated, so make sure to account for this and select a supply with a higher current rating than needed.
- [ ] 20AWG (or larger diameter, depending on length & number of modules) wire for 12v power and ground

OR, for 13-36 modules:

- [ ] 22AWG wire for 3.3v power (gauge is not critical as this is low-current; solid wire is preferable to stranded for use with screw terminals)
- [ ] 12V power supply capable of *at least* **1.5A for every 6 modules**, plus some margin. *You must connect the power supply to the screw terminals of the first Chainlink Driver* ***directly***. Do not use the Chainlink Buddy’s barrel jack connector with more than 12 modules, as it cannot handle the current requirements!
    - Assume that the current ratings on supplies sold by Amazon, AliExpress, etc are overstated, so make sure to account for this and select a supply with a higher current rating than needed.
- [ ] 16AWG (or larger diameter, depending on length & number of modules) wire for 12v power and ground

OR, more than 36 modules:
> [!WARNING]
> Special considerations apply for displays with more than 36 modules! You must have a strong understanding of the limitations and risks involved with high-current DC power supplies, and should take all reasonable precautions to protect against damage/injury. Make sure to read the Chainlink Driver user guide for more info if you will be building a [large display](../ElectronicsGuide.md#Large-displays) with 36+ modules.

## That’s all!

For instructions on assembly, see the [Splitflap v2 Assembly Guide](Assembly.md) and [Chainlink Driver Electronics User Guide](../ElectronicsGuide.md) 

----------

Link disclosure: As an Amazon Associate I earn from qualifying purchases at no cost to you.

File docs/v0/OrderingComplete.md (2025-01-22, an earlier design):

# Splitflap v0 Comprehensive Ordering Guide
[<< Back to Documentation Index](../DocumentationIndex.md)

The instructions below will walk you through ordering all the parts (excluding common tools) needed to build a splitflap v0.7 display with **6 modules** using the latest Chainlink electronics.

Ready to assemble? Jump ahead to the [Assembly Guide](Assembly.md)

If you have any questions, please feel free to reach out to me (scott@bezeklabs.com). Or, join the [Discord server](https://discord.gg/wgehm3PcrC), to discuss or ask questions from the wider split-flap community!

😩 Feeling overwhelmed by this document? I don’t blame you, there’s a LOT here… So I put together a much shorter document that favors simplicity over comprehensiveness/lowest-cost,
for people in the US: [+Splitflap Ordering (the “easy” route)](OrderingEasy.md) 

💡 These instructions have been updated for the “Chainlink” electronics system, which is recommended over the legacy (circa 2016) “Classic Controller” for all new builds due to easier assembly and more flexibility. If you’re looking for the older Classic Controller instructions, they’ve been moved to the [Appendix](#appendix-c-legacy-classic-controller).

1. [Order laser-cut parts](#order-laser-cut-parts)
3. [Order electronics](#order-electronics-chainlink)
2. [Order hardware](#order-misc-hardware)
4. [Appendix A: Older laser-cut file versions](#appendix-a-older-laser-cut-file-versions)
5. [Appendix B: Hall effect sensor options](#appendix-b-hall-effect-sensor-options)
6. [Appendix C: Legacy Classic Controller](#appendix-c-legacy-classic-controller)
    1. [Classic-specific hardware](#classic-specific-hardware)
    2. Classic Controller
        1. [Order controller PCB](#order-controller-pcb-classic)
        2. [Order sensor PCBs](#order-sensor-pcbs)
        3. [Order electronic components](#order-electronic-components-classic)

----------
# Order laser-cut parts

There are many places you can get laser-cut parts, but I’ve personally used Ponoko and Elecrow for ordering shipped to the US with an easy online-only process. I’ve been using Ponoko for several years and they offer a lot of different material options and good quality, but recently I’ve found Elecrow’s laser-cutting service, which can be **significantly** cheaper with good quality (though very limited material options).

The front face of each module is approximately **82.6mm wide** and **147.8mm tall**.

For advanced makers: if you want to cut a single front panel that will be shared by an entire row (or grid) of modules, there is a script to do so with lots of configurable options like spacing, rows/cols, and even has a mode for generating geometry for CNC routing with necessary “dog-bones” applied to inside corners — see `generate_combined_front_panel.py`

💡 Note: v0.7 laser-cut parts are not dimensionally compatible with older v0.6 or v0.5 modules! If you’re extending an older display, make sure to use the older v0.6 files
[archived at the bottom of this document](#older-v06-laser-cut-files) rather than the newer v0.7 files linked here.

## Ponoko
    - 1 module
        - 3mm MDF: https://github.com/scottbez1/splitflap/releases/download/v0.7/3d_laser_vector-ponoko-3mm-mdf_1x.svg [177.42mm x 173.37mm]
        - 3mm Acrylic: https://github.com/scottbez1/splitflap/releases/download/v0.7/3d_laser_vector-ponoko-3mm-acrylic_1x.svg [177.26mm x 173.05mm]
    - 4 modules
        - 3mm MDF: https://github.com/scottbez1/splitflap/releases/download/v0.7/3d_laser_vector-ponoko-3mm-mdf_4x.svg [354.84mm x 346.74mm]
        - 3mm Acrylic: https://github.com/scottbez1/splitflap/releases/download/v0.7/3d_laser_vector-ponoko-3mm-acrylic_4x.svg [354.52mm x 346.10mm]

- Go to [Ponoko](https://www.ponoko.com/) and sign up for an account.
- [Upload](https://www.ponoko.com/designs) the SVG file from above. Confirm the dimensions match the values above, and check that blue lines are set for “Cutting” and black fill is set for “Area Engraving” (or turn this off to skip engraved features)


- Select a material - [MDF](https://www.ponoko.com/materials/mdf-fiberboard) or [Acrylic](https://www.ponoko.com/materials/black-matte-acrylic) are recommended — choose 3.0mm (0.12 inches) thickness. Make sure to check the material’s maximum size against the dimensions provided next to the file links above; some materials may be too small to order the 4x versions.

💡 **Important note if ordering** **Matte 1-Side** ****acrylic at Ponoko: you ***must*** immediately send special instructions to Ponoko after placing your order, requesting to have the design engraved on the *glossy* side. This will result in the design being correctly cut so the matte surface will be on the exterior of the display when assembled. From Ponoko support (as of 2021-05-13): 

> The matte is [by default] cut with the matte side up (so engraving happens on this side as well).
> 
> If you would like to place an order and have us engrave on the glossy side, just **reply to the order confirmation page** with your request and we'll be sure to make note in the order details.

## Elecrow

Elecrow will cut 5 copies of the design per order from “wood” (unspecified type), for $14.55 + shipping. I think you’d be hard-pressed to find a cheaper deal (but let me know if you do!).

From experience it appears to be a 3-ply construction, with thin veneers on the front and back and some kind of very lightweight wood core. The thickness came out slightly undersized, at ~2.8mm rather than 3mm as specified. The finish and material is not as nice as Ponoko’s MDF (my order had visible scorch marks near cuts), so keep that in mind when deciding.

- Download the appropriate file:
    - 3mm wood: https://github.com/scottbez1/splitflap/releases/download/v0.7/3d_laser_vector-elecrow-3mm-wood_1x.zip
    - 3mm acrylic: [not yet tested. If you try this, I’d recommend starting with the Ponoko 3mm acrylic file from above; let me know which file you used and how it turns out - under/oversized, etc and I will use that feedback to generate a recommended file in the future]
- Go to https://www.elecrow.com/5pcs-wood-laser-cutting-service.html
- Select “20cm Max * 20cm Max(Thickness: 3.0mm)” for the dimension
- Upload the .zip file you downloaded above
- Add to cart and check out


- For shipping, I would suggest avoiding “Registered Airmail” - it took well over a month and tracking was terrible; my second order with ShenZhenDHL just took a couple days. 
- Here are example shipping fees to California, as of 2020-06-1


----------
# Order electronics (Chainlink)

The Chainlink system is a newer electronics system based around the more powerful ESP32 microcontroller (which adds things like wifi support) and incorporates learnings from the earlier Classic Controller. New development is focused on the Chainlink system.

The basic pieces that you’ll need for a Chainlink system:

- **Chainlink Driver board** (1 for every 6 split-flap modules you want to control)
- **Chainlink Buddy** + **ESP32** (1 for the whole display, regardless of size)
- **Sensors** (1 for every split-flap module)

The easiest and best-supported approach is to purchase each of those items from the Bezek Labs Etsy store (US only) - I’ve set up the store so that items comes with the necessary accessories, meaning there are fewer things you need to track down and purchase separately from different suppliers. Proceeds also help fund continued development of the project!

💡 See the [Chainlink User Guide](../ElectronicsGuide.md) for more info about different configurations.

## Order Chainlink Driver


The Chainlink Driver is what drives up to 6 split-flap modules. Multiple Chainlink Drivers can be chained (hence the name!) to create much larger displays (I have created a 108-module display using 18 Chainlink Driver boards).

The Chainlink Driver uses mostly surface-mount components so it’s optimized for factory production moreso than hand-soldering (though you can of course do that if you’d like)

[**Recommended] Option 1: Purchase fully-tested PCBA on Etsy (US shipping only)**
I sell mostly-pre-assembled Chainlink Driver boards in the Bezek Labs Etsy store:

https://bezeklabs.etsy.com/listing/1123280069/splitflap-chainlink-driver-v11

(includes accessories: connectors, ribbon cable)

These have all the tricky surface-mount components already soldered for you. You’ll just need to solder the through-hole connectors, which are pretty easy.

Every single board that I sell goes through a rigorous 100% functionality test which validates every single motor output, sensor input, LED, and data line works as expected, using a custom test jig I developed.

This option also includes all the connectors and ribbon cable you’ll need, so you don’t need to order anything separately!

And, if you want to make sure you get the right 28byj-48 motors instead of just ordering on AliExpress and hoping for the best, I’ve added an option on Etsy to include 6x motors with your Chainlink Driver order! Yes, they’re more expensive than ordering on AliExpress directly, but they’ll ship quickly and you’ll know you’re getting good motors. 

**Option 2: Purchase assembled Chainlink Driver from JLCPCB, and purchase connectors and ribbon cable separately**
The Chainlink Driver design is optimized for JLCPCB assembly, so it’s mostly a drag-and-drop process, but you’ll need to carefully understand the options you select. Most importantly, if JLCPCB is out of stock of a component, *they will continue to build your order and simply omit that component!* So be careful to check all warnings or notices that appear when ordering.

Note that JLCPCB assembly involves a number of fixed costs (such as $3 per unique part) which make larger quantities a better value. 

Download the following 3 items from the latest Chainlink Driver release (v1.1):

- gerber files (for the PCB)
- BOM (specifies which components are needed for assembly)
- CPL (specifies placement locations for components)

To order:



- Go to JLCPCB https://cart.jlcpcb.com/quote
- Upload gerber zip
- Select your quantity, PCB color
- Confirm other parameters:
    - Dimensions: 30.48 x 198.12
    - PCB Thickness: 1.6
    - Outer Copper Weight: 1oz



- Select SMT Assembly
    - Assemble top side
    - Select your quantity to assemble
    - Tooling holes: select **Added by Customer** (these are included in the design already, so you do not need JLC to add them)
    - Confirm



- Upload BOM File
- Upload CPL (csv) file



- Review parts
    - ⚠️ Make sure you check this step carefully, as any parts that are out of stock will simply be omitted! ⚠️ 
    - “No part selected” is *normal* for several connectors that will not be assembled by JLCPCB (see below) - these will be “J”-prefixed designators such as “Motor A”, “Sensor C”, or “Input” or “Output”

- Review parts placement
- Save to Cart
- Checkout (note that JLC does NOT reserve parts until you’ve checked out and paid your order, so if stock is low there is a chance parts will be missing if you wait to pay!)

To keep assembly costs lower, and to avoid fluctuating stock issues for parts that are readily available elsewhere and easy to hand-solder, the design files for assembly *do not include the following parts*, which you should order separately (or you can use the LCSC part numbers below to select them during the Review Parts step and pay the additional costs for assembly):

- 2x IDC shrouded connectors, 2x4, 2.54mm spacing, e.g. JLC/LCSC [C601937](https://lcsc.com/product-detail/IDC-Connectors_JILN-321008SG0ABK00A01_C601937.html), or on [Digi-Key](https://www.digikey.com/en/products/detail/adam-tech/BHR-08-VUA/9832409)
- 6x JST XH 5 pin connectors, e.g JLC/LCSC [C161872](https://lcsc.com/product-detail/Wire-To-Board-Wire-To-Wire-Connector_JST-Sales-America-B5B-XH-AM-LF-SN_C161872.html). or [C378947](https://lcsc.com/product-detail/Wire-To-Board-Wire-To-Wire-Connector_JST-Sales-America-B5B-XH-A-BK-LF-SN_C378947.html), or LCSC [C157991](https://lcsc.com/product-detail/Wire-To-Board-Wire-To-Wire-Connector_JST-Sales-America-B5B-XH-A-LF-SN_C157991.html), or on [Digi-Key](https://www.digikey.com/en/products/detail/jst-sales-america-inc/B5B-XH-AM-LF-SN/1651037)
- 6x 3-pin male headers, 2.54mm spacing, e.g. JLC/LCSC [C49257](http://), or on Digi-Key [3-pin](https://www.digikey.com/en/products/detail/sullins-connector-solutions/PREC003SAAN-RC/2774851) or purchase [40-pin](https://www.digikey.com/en/products/detail/sullins-connector-solutions/PREC040SAAN-RC/2774814) and break apart, (or readily available in bulk on Amazon, etc)

In order to connect your Chainlink Driver to your microcontroller (or to another Chainlink Driver in a chain), you’ll also need an IDC ribbon cable + connectors:

- 1x 8 conductor 1.27mm spacing ribbon cable (45cm recommended minimum length for chaining), [e.g. on Digi-Key](https://www.digikey.com/en/products/detail/w%C3%BCrth-elektronik/63910815521CAB/8324550)
- 2x IDC connectors, e.g. LCSC [C601910](https://lcsc.com/product-detail/IDC-Connectors_JILN-531408YBS0BW01_C601910.html), or on [Digi-Key](https://www.digikey.com/en/products/detail/adam-tech/FCS-08-SG/9832361)

You may get an email from JLCPCB after placing your order, asking to double-check the orientation of the screw terminals. See images below for the correct orientation: the wires would go *over* the Power labels on the PCB to be inserted into the front of the screw terminals.

✅ 3d model of the design with CORRECT screw terminal orientation
✅ Confirmation email from JLCPCB, showing CORRECT screw terminal orientation. If the image they send you looks like this, go ahead and confirm it!
🚫 INCORRECT: If it looks like this, it’s facing the WRONG way!

**Option 3: Purchase bare PCB, components, and hand-assemble**
This is an advanced option which will require hand-soldering surface mount components. While the components aren’t tiny (ICs are SOIC packages and passives are 0603), it will require some skill and patience.

You might also consider ordering a stencil and reflow soldering the components yourself. However, be aware that the PCB is long and thin so it is prone to warping when heated, so you may have difficulty if you plan to use a hot plate rather than an oven.

Follow the instructions from Option 2 above for ordering the PCBs, and instead of selecting assembly, you can use the BOM file to order all the components yourself. The BOM file uses LCSC part numbers.
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

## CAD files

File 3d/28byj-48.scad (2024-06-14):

/*
   Copyright 2015-2018 Scott Bezek and the splitflap contributors

   Licensed under the Apache License, Version 2.0 (the "License");
   you may not use this file except in compliance with the License.
   You may obtain a copy of the License at

       http://www.apache.org/licenses/LICENSE-2.0

   Unless required by applicable law or agreed to in writing, software
   distributed under the License is distributed on an "AS IS" BASIS,
   WITHOUT WARRANTIES OR CONDITIONS OF ANY KIND, either express or implied.
   See the License for the specific language governing permissions and
   limitations under the License.
*/

28byj48_chassis_radius = 28/2;
28byj48_chassis_height = 19;
28byj48_shaft_offset = 8;
28byj48_mount_outer_radius = 3.5;
28byj48_mount_hole_radius = 4.2/2;
28byj48_mount_center_offset = 35/2;
28byj48_mount_bracket_height = 0.8;

28byj48_shaft_collar_radius = 9.4/2;
28byj48_shaft_collar_height = 1.5;

28byj48_shaft_radius = 5/2;
28byj48_shaft_height = 10;
28byj48_shaft_slotted_width = 3;
28byj48_shaft_slotted_height = 6;

28byj48_backpack_width = 14.6;
28byj48_backpack_extent = 18; // seen values from 17-18
28byj48_backpack_height = 16;

// Exports for use in other files:
function 28byj48_mount_bracket_height() = 28byj48_mount_bracket_height;
function 28byj48_shaft_radius() = 28byj48_shaft_radius;
function 28byj48_shaft_collar_radius() = 28byj48_shaft_collar_radius;
function 28byj48_mount_center_offset() = 28byj48_mount_center_offset;
function 28byj48_chassis_radius() = 28byj48_chassis_radius;
function 28byj48_shaft_offset() = 28byj48_shaft_offset;
function 28byj48_chassis_height() = 28byj48_chassis_height;
function 28byj48_backpack_extent() = 28byj48_backpack_extent;

// Basic 28BYJ-48 model based on various dimensioned drawings.
// Origin is centered on the shaft, on the front face of the motor, with the shaft in the +z direction
module Stepper28BYJ48() {
    $fn = 60;

    eps = 0.01;

    gray = [0.7, 0.7, 0.7];
    gold = [1, 0.843, 0];
    blue = [0, 0, 1];

    module mounting_holes() {
        linear_extrude(height=28byj48_mount_bracket_height) {
        difference() {
            hull() {
                translate([28byj48_mount_center_offset, 0]) {
                    circle(r=28byj48_mount_outer_radius);
                }
                translate([-28byj48_mount_center_offset, 0]) {
                    circle(r=28byj48_mount_outer_radius);
                }
            }

            translate([28byj48_mount_center_offset, 0]) {
                circle(r=28byj48_mount_hole_radius);
            }
            translate([-28byj48_mount_center_offset, 0]) {
                circle(r=28byj48_mount_hole_radius);
            }
        }
        }
    }

    module shaft_collar() {
        cylinder(r=28byj48_shaft_collar_radius, h=28byj48_shaft_collar_height + eps);
    }

    module shaft() {
        color(gold) {
            difference() {
                cylinder(r=28byj48_shaft_radius, h=28byj48_shaft_height);
                translate([-(28byj48_shaft_radius + eps), 28byj48_shaft_slotted_width / 2, 28byj48_shaft_height - 28byj48_shaft_slotted_height]) {
                    cube([(28byj48_shaft_radius+eps)*2, 28byj48_shaft_radius, 28byj48_shaft_slotted_height+eps]);
                }
                translate([-(28byj48_shaft_radius + eps), - 28byj48_shaft_radius - (28byj48_shaft_slotted_width / 2), 28byj48_shaft_height - 28byj48_shaft_slotted_height]) {
                    cube([(28byj48_shaft_radius+eps)*2, 28byj48_shaft_radius, 28byj48_shaft_slotted_height+eps]);
                }
            }
        }
    }

    module chassis() {
        color(gray) {
            translate([0, 0, -28byj48_chassis_height]) {
                cylinder(r=28byj48_chassis_radius, h=28byj48_chassis_height);
            }
            translate([0, 0, -28byj48_mount_bracket_height - eps]) {
                mounting_holes();
            }
            translate([0, 28byj48_shaft_offset, -eps]) {
                shaft_collar();
            }
        }
    }

    module backpack() {
        color(blue) {
            translate([-28byj48_backpack_width/2, 0, -28byj48_backpack_height - eps]) {
                cube([28byj48_backpack_width, 28byj48_backpack_extent, 28byj48_backpack_height]);
            }
        }
    }

    translate([0, -28byj48_shaft_offset, 0]) {
        chassis();
        translate([0, 28byj48_shaft_offset, 0]) {
            shaft();
        }
        translate([0, -28byj48_backpack_extent, 0]) {
            backpack();
        }
    }
}

// Example usage:
Stepper28BYJ48();

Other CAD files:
3d/global_constants.scad
3d/sensor_pcb_dimensions.scad
3d/assert.scad
3d/color_util.scad
3d/combined_front_panel.scad
3d/flap.scad
3d/flap_3dp.scad
3d/flap_characters.scad
3d/flap_container.scad
3d/flap_dimensions.scad
3d/flap_fonts.scad
3d/font_generator.scad
3d/label.scad
3d/m4_dimensions.scad
3d/pcb.scad
3d/pcb_case.scad
3d/projection_renderer.scad
3d/punch_jig.scad
3d/rough7380.scad
3d/scoring_jig.scad
3d/shapes.scad
3d/splitflap.scad
3d/spool.scad
3d/tools/classic_pcb_mount.scad
3d/tools/connector_case.scad
3d/tools/flap_container.scad
3d/tools/mounting_bracket.scad
3d/tools/punch_jig.scad
3d/tools/scoring_jig.scad

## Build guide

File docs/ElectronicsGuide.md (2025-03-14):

# Chainlink Driver Electronics User Guide
[<< Back to Documentation Index](DocumentationIndex.md)

# Intro

If you’re just getting started and want to learn more about the Chainlink Driver, jump to the [bottom of this document](#what-is-the-chainlink-driver) which includes some more background and general info.

Please let me know if you have any questions or suggestions on how to improve these instructions - feel free to open a pull request or joing the [community Discord server](https://discord.gg/wgehm3PcrC)

Building a split-flap display? I would love to hear from you and see photos/videos of your project in progress or completed! This project has been a hobby of mine for a few years and the coolest part by far is hearing from other people making their own and seeing them in action. Feel free to shoot me an email at scott@bezeklabs.com 🙂 or, [join the Discord server](https://discord.gg/wgehm3PcrC), to share and discuss with the wider split-flap community!

# 1. Gather the parts
- Chainlink Driver PCB assembly (see [appendix](#appendix) for ordering info)
- Connectors (all included with the Chainlink Driver boards I sell on Etsy)
    - 6x JST XH 5-pin
    - 6x 3-pin male headers
    - 2x 8-pin 2-row shrouded IDC connectors
- Wires
    - 8-pin 1.27mm ribbon cable, and IDC connectors for each end (included with the Chainlink Driver boards I sell on Etsy)
    - 3.3v power wire
        - e.g. 22AWG solid hookup wire
    - 12v power/ground wires
        - 20AWG up to 14AWG depending on number of modules
- 12V Power supply (see [appendix](#appendix) for more info)
- ESP32
Chainlink Buddy [T-Display]

    - The [TTGO T-Display](https://amzn.to/3kHwhMm) [affiliate links help support this project at no cost to you, or use a [non-affiliate link](https://www.amazon.com/LILYGO-T-Display-Arduino-Development-CH9102F/dp/B099MPFJ9M) if you’d prefer] is the recommended ESP32 board, which includes a 240x135 LCD that the splitflap firmware supports out of the box. (Also available on [aliexpress](https://www.aliexpress.com/item/33048962331.html), which may be cheaper)
    - An optional [Chainlink Buddy [T-Display]](https://bezeklabs.etsy.com/listing/1109357786/splitflap-chainlink-buddy-t-display) is also highly recommended for most users, which makes it easy and clean to connect a T-Display to the Chainlink Driver.
    - If you want to use an ESP32 module other than a T-Display, a [Chainlink Buddy [Breadboard]](https://bezeklabs.etsy.com/listing/1123863267/splitflap-chainlink-buddy-breadboard) may be helpful in lieu of the T-Display Buddy. See the [appendix](#appendix) for more info on using other ESP32 modules.

# 2. Finish assembling the PCB
- Insert and solder the connectors as shown. Note that both of the IDC connectors on the ends face the same way - notches facing left.


- Insert the ribbon cable into a connector as shown, and *gently* clamp shut with a vise or pliers. Repeat with the other connector on the opposite end, making sure that both connectors face the **same** way - notches facing left.


- Not recommended, but you can optionally install the strain relief on the connectors (included with Bezek Labs Chainlink Driver boards): fold the ribbon cable back over the connector and install the plastic piece to clamp it down until it clicks. You’ll sacrifice some cable length and end up with a bulkier/taller connector, so I don’t think it’s worthwhile, especially since your cables shouldn’t be moving around much anyway.

# 3. Assemble the Chainlink Buddy
- Solder the connectors into place (make sure the IDC connector notch faces the left, as indicated on the PCB)

## T-Display Buddy



On the T-Display itself, you will solder the 2 rows of male headers (included in the box) to the T-Display, and then the whole module will plug into the matching female headers you soldered on the Buddy board.

You may notice a few empty spaces in the lower left of the T-Display Buddy PCB labeled C1 and C2 along with 3 through-holes; don’t worry, those are optional components and not needed for a basic setup. See [Standalone T-Display operation](#8-optional-standalone-t-display-operation) for more info.



Note: the T-Display often comes with a small Red/Black wiring harness with connector as well; it is unused with the Chainlink Buddy and can be discarded.

## Breadboard Buddy (alternative to T-Display Buddy)

If you’d prefer to use a different ESP32 module, you can use the Breadboard Buddy PCB to easily adapt the IDC cable to a breadboard.




# 4. Connect Chainlink Driver to Chainlink Buddy

We’ll start by connecting and testing just the Chainlink Driver, without connecting a power supply or any modules’ motors or sensors. We’ll add those later, after confirming that the basic electronics work.

## T-Display
- Connect the ribbon cable from the Chainlink Buddy’s **Output** to the Chainlink Driver’s **Input**
- Connect a wire from the Chainlink Driver’s “Logic 3.3-5V” screw terminal to the “3.3V” screw terminal on the Chainlink Buddy
- Connect a wire from the Chainlink Driver’s “GND” screw terminal to the “GND” screw terminal on the Chainlink Buddy
- Connect a wire from the Chainlink Driver’s “Motor 5-12v” screw terminal to the “12V” screw terminal on the Chainlink Buddy
- ⚠️  Never connect a battery to the T-Display’s battery connector (small white connector on the bottom of the TTGO T-Display module) when using the Chainlink Buddy! 


## Breadboard (if you’re not using the T-Display Buddy)
- Connect the ribbon cable from the Chainlink Buddy’s **Output** to the Chainlink Driver’s **Input**
- Connect a wire from the Chainlink Driver’s “Logic 3.3-5V” screw terminal to a 3.3v supply on your breadboard
- Connect a wire from the Chainlink Driver’s “GND” screw terminal to your breadboard’s ground rail
- Connect the 5 pins to your ESP32. See the [appendix](#appendix) for more info. Default pin assignments are:
    - Clock: 33
    - Motor Data: 32
    - Sensor Data: 39
    - Latch: 25
    - GND: ground


# 5. Install firmware

**Download and install** [**Microsoft Visual Studio Code**](https://code.visualstudio.com/)

**Install the Platform IO extension**

**Clone the repository**
Choose “Clone Git Respository” from the VS Code welcome page and then paste the git repo URL: `https://github.com/scottbez1/splitflap.git` 




When prompted, choose to open the cloned repository.

You may need to choose to “Trust” the folder to allow the Platform IO extension to run.



You’ll need to configure NUM_MODULES in platformio.ini to match the number of modules supported by the Chainlink Drivers you have connected. So for a single Chainlink Driver, set it to 6.

    [env:chainlink]
    extends=esp32base
    build_flags =
        ${esp32base.build_flags}
        -DCHAINLINK
        -DNUM_MODULES=6

- (If you’re *no*t **using a T-Display, see the [appendix](#appendix) for a few more changes you’ll need to make at this point)
- Mac Users: you will likely need to install updated drivers for the CH9102 USB-serial adapter used on newer versions of the ESP32 T-Display: https://learn.adafruit.com/how-to-install-drivers-for-wch-usb-to-serial-chips-ch9102f-ch9102/mac-driver-installation

To upload code to the ESP32 T-Display from VS Code, you’ll need to (see screenshot below):

> 1) Open the Platform IO sidebar (click the alien icon on the left)
> 2) Click the “env” button at the bottom of the window and then in the dropdown at the top of the screen…
> 3) …select “env:chainlink” as the environment - this will set up code completion and syntax highlighting for the ESP32
> 4) in the  Platform IO sidebar, expand the “General” section, and click `Upload and Monitor` 


- If you reset the ESP32, you should see the LEDs on the Chainlink Drivers blink quickly and a message in the serial monitor that loopbacks are ok. If you see a loopback error message, troubleshoot that before continuing.

*NOTE*: Make sure to exit the terminal window before starting calibration.  Otherwise, you might get an error as both should not be running at the same time.

# 6. Connect modules and power
## Motors
- Plug into the white connectors. Note that module connections are laid out from *right-to-left* since the Chainlink Driver PCB is intended to sit *behind* the modules, so the first module plugs into position “A” on the **right** side of the PCB
## Sensors


- Plug sensor cable into corresponding 3-pin header
- Ground (black) should be on the left (toward the “Output” side), labeled “-”
- Signal (usually white) should be on the right (toward the “Input” side), labeled “S”
## 

## Power

The ESP32 and 3.3v electronics on the Chainlink Drivers are typically powered by the USB connection to a computer. 12V power for the motors is supplied via a separate power supply.

> Note: avoid leaving 12V power on when the ESP32 is not running! Doing so could damage your motors or worse, as the motor coils could be "stuck on" if the ESP32 is not running.

**T-Display**

- You can plug a DC 12v barrel jack into the T-Display Buddy when using 1 or 2 Chainlink Drivers
- ⚠️ For more than 2 Chainlink Drivers, the barrel jack cannot handle enough current, so you should instead connect your power supply directly to the Motor Power terminals of the first Chainlink Driver. Make sure you are using the [appropriate wire gauge](#power-supply-tips), and [never chain power to more than 6 Chainlink Drivers](#large-displays)

[Wiring diagram](img/chainlinkWiringv1.1.pdf)

**Breadboard**

- Connect your power supply directly to the Motor Power terminals of the first Chainlink Driver. Make sure you are using the [appropriate wire gauge](#power-supply-tips), and [never chain power to more than 6 Chainlink Drivers](#large-displays)

[Wiring diagram](img/chainlinkWiringv1.1.pdf)

# 7. (Optional) Adding more Drivers

You can easily chain several Chainlink Drivers by connecting ribbon cables, and adding additional power wires using the second set of power screw terminals (there are 2 terminals each for the 3.3v, ground, and 12v power), but make sure to follow this rule:

    ⚠️ Never chain power to more than 6 Chainlink Drivers in a row ⚠️ 

The screw terminals have a limited current rating (10A on the ones sold by Bezek Labs), so **using more than 6 Chainlink Drivers will require power to be wired differently**. See [+Chainlink Driver v1.1 Electronics User Guide: Large-displays](#large-displays) below for more info on wiring large displays.

# 8. (Optional) Standalone T-Display operation

Under the normal configuration, you would power the motors with a 12V supply and separately the T-Display is powered via its 5V USB connection to a computer.

However, it’s possible to omit the USB connection for a completely standalone setup, powered by the 12V motor supply. This works well when you’re using the Wifi capabilities of the T-Display, for example to poll an HTTP(s) API or listen to an MQTT topic.

To do this, you’ll need to add 3 components to the Chainlink Buddy [T-Display] (must be purchased separately):

- 5V switching regulator
    - [Mornsun K7805-500R3](https://www.digikey.com/en/products/detail/mornsun-america-llc/K7805-500R3/13168189) is one recommended option, but any **switching** regulator module in a 7805 form-factor rated for 500mA+ should work - just double-check the capacitor requirements from the datasheet for the input (C1) and output (C2). A classic 7805 linear regulator is NOT recommended.
- 22uF 1206 ceramic capacitor - 16V - install to C2
    - e.g. [CL31A226MOCLNNC](http://)
- 10uF 1206 ceramic capacitor - 50V - install to C1
    - e.g. [CL31A106MBHNNNE](https://www.digikey.com/en/products/detail/samsung-electro-mechanics/CL31A106MBHNNNE/5961220)
    - or just get 2 22uF capacitors and use for both C1 and C2, but make sure to choose one rated for 25V+, e.g. [CL31A226KAHNNNE](https://www.digikey.com/en/products/detail/samsung-electro-mechanics/CL31A226KAHNNNE/3888705)



----------
# Appendix
## What is the Chainlink Driver?


The Chainlink Driver is an updated control board for splitflap displays, building on lessons learned from the Classic Controller.

There were 2 main goals in designing it:

- support for controlling a *LOT* of splitflaps
- low cost and ease of purchasing pre-assembled boards - it’s mostly SMD instead of through-hole

Each Chainlink Driver PCBA contains all the power and signal electronics to drive the stepper motors and read the home position sensors for **up to six** modules, and can be trivially chained together to control 100+ splitflap modules using just 4 pins of an ESP32.

https://www.youtube.com/watch?v=g9EPabcxBsM&

## Where to buy a Chainlink Driver?


The design is open source, so you can order them directly from a PCB manufacturer using the design files provided, but I also [sell them in my Bezek Labs Etsy store](https://bezeklabs.etsy.com/listing/1123280069/splitflap-chainlink-driver-v11) within the US.

Buying them from my store has the advantage of being [100% functionality tested after assembly using a custom testbed](https://twitter.com/scottbez1/status/1414986069586575360), and it helps support further development and prototyping of this project. I also include all the connectors and a ribbon cable for your convenience.

If you’d like to order them directly from a PCB manufacturer, the designs are optimized for JLCPCB’s Assembly service (not sponsored or affiliated, but they do have extremely cheap assembly as long as you stick to a limited set of components available in their part library). Note that the BOM does *not* include many of the connectors because there is a $3-per-unique-part fee, and since you’ll need to order the ribbon cable separately anyway this can keep your costs lower for small orders.

## Power supply tips

You’ll need a 12V supply with a current rating that depends on the number of modules you’ll be controlling (and even the particular motors you’re using, as not all 28byj-48 motors have the same coil resistance).

A good starting assumption is that each motor will draw 0.25A each (typical estimate for motors with 100 ohm half-winding resistance), but you should always test your motors, and include a safety margin.

So for every Chainlink Driver you use, plan for at least 1.5A capacity, but many cheap power supplies have questionable/overstated ratings, so you probably want 2A minimum.

For a large display, I’ve used a [Mean Well LRS-350-12](https://amzn.to/3cdjuwD) [affiliate links help support this project at no cost to you, or use a [non-affiliate link](https://www.amazon.com/MEAN-WELL-LRS-350-12-Computer-Project/dp/B07VTLJS18) if you’d prefer] which I found to easily supply 22+ amps with little voltage ripple.

Make sure to select appropriate gauge copper wire for power (this includes the GND wires!). The current along a chain of Chainlink Driver boards adds up quickly!

I also recommend adding fuses near the power supply as an added layer of protection, especially on larger displays. The LRS-350-12 mentioned above is capable of supplying 29A *continuously* which is a lot of current and potentially destructive in case of a fault. Since each power branch (see advanced wiring diagram) will use less than this, you should protect each branch with its own appropriately-sized fuse.

Make sure to buy power wiring from a reputable seller with a trustworthy supply chain (e.g. an electronics supplier or a big box hardware store, not AliExpress or Amazon). 
Unfortunately, as the cost of copper has gone up it’s [more common to find wire using other metals](https://www.youtube.com/watch?v=15sMogK3vTI) which may not meet its advertised specs.

## Using a different ESP32 module

In theory, any ESP32 module *with 2 cores* (i.e. *not* based on an ESP32-**S2**) should work. Most common WROOM or WROVER-based modules can work.

However, not all cheap modules are well designed (some are not breadboard friendly, some have poor power design causing brownouts during wifi/ble, etc), so I’ve found the T-Display to be a great default. You do lose a few IO pins to the LCD, but the Chainlink firmware supports the LCD out of the box and I think you’ll find it handy for debugging.

That said, if you do use another module here’s what you need to know:

1. You probably want to disable the display code to free up those pins and avoid wasting CPU cycles.  Do this by changing `-DENABLE_DISPLAY=1` to `-DENABLE_DISPLAY=0` in platformio.ini
2. Since the ESP32 has a GPIO matrix, you can change the pin assignments easily (see spi_io_config.h), but you do need to [avoid certain reserved functions](https://www.youtube.com/watch?v=LY-1DHTxRAk) so I recommend using the defaults unless you have a good reason not to.

## Large displays

The Chainlink system can support large displays, but please be aware that more care needs to be taken as the size of the display (and therefore, the power supply and electronics involved) increases. 

If you are wiring more than 6 Chainlink Driver boards, **only data connections should form a continuous chain**! This is shown in blue on the diagram below.

The power should branch into **separate chains of up to 6 Drivers** (or fewer if your motors require more current).

Chaining power continuously like the data would overload the screw terminals and wires at the beginning of the chain, potentially causing damage/fire. Note how the yellow and black wires in the diagram below branch *at the power supply* and do not continue past each sub-chain of 6 Drivers.

[Advanced wiring diagram](img/chainlinkWiringAdvanced.pdf)

I would also strongly recommend adding additional safety measures with a display of this size, considering the total power involved. For instance:

- Fuses for each branch of power
- Real-time voltage & current monitoring, and individual load switches for each “branch” to detect and respond to faults
- Relay controlling mains input to 12V power supply (intentionally redundant with 12V branch load switches)

The Chainlink Base (taking the place of the Chainlink Buddy in the system) is one possible approach to some of these measures, but it is not officially supported/recommended.

Make sure you consult a qualified electrician/engineer to review all designs (including splitflap project schematics and PCBs), and be sure to follow applicable regulatory codes.

----------

Link disclosure: As an Amazon Associate I earn from qualifying purchases.
(I’ve also chosen to include non-affiliate links next to every affiliate link should you prefer to avoid using affiliate links)

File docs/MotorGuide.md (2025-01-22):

# 28BYJ-48 Motor Buying Guide
[<< Back to Documentation Index](DocumentationIndex.md)

There are a *lot* of different motors that go by the same “28BYJ-48” name.

If you want to be certain you're getting good motors (and you're in the US), you can opt to add motors to your purchase of a [Chainlink Driver](https://bezeklabs.etsy.com/listing/1123280069/splitflap-chainlink-driver) from the [Bezek Labs](https://bezeklabs.etsy.com) store.
I qualify each batch of motors I receive so you can be sure they'll work great (or I'll replace/refund them).

### Latest AliExpress recommendation (as of 2024-06-25)

As of 2024-06-25, I recommend SeasBoat Store as a fairly reliable AliExpress seller over the last few years, having ordered many hundreds of motors from them myself (but as always, they may send you different motors, so it’s no guarantee).

They have 2 listings available:
- a [“Choice” listing](https://s.click.aliexpress.com/e/_mKVNenq) that is more expensive individually, but qualifies for free shipping over $10 (or use this [non-affiliate link](https://www.aliexpress.us/item/2255800976774653.html)). This may be chepaer for a smaller quantity of motors.
- a [non-Choice listing](https://s.click.aliexpress.com/e/_m0W7bZq) with a lower per-unit cost but with a shipping charge (or use this [non-affiliate link](https://www.aliexpress.us/item/3256807022196320.html)). This is likely cheaper for larger orders.

Make sure you select the “12V” option when adding to your cart!

Depending how many motors you’re ordering and where you are shipping to, you may want to use one listing or the other.

## What's different about different "28BYJ-48" motors?

The two areas of variation are:

- gear ratio
    - common values are 16.032:1, 64:1, and 63.68395:1
- coil resistance
    - I’ve seen variants ranging from 26 ohms to 185 ohms

(For more background reading, see [Graham Wideman’s detailed post](http://web.archive.org/web/20180528105141/http://grahamwideman.wikispaces.com/Motors-+28BYJ-48+Stepper+motor+notes), though it does not even cover all the variants I have seen)

Both of those factors - gear ratio and coil resistance - have a pretty big impact on output torque, max speed, and control sequence (steps per revolution), but unfortunately most sellers don’t provide that info, or worse, they’ll often provide **incorrect info**.

Making things worse, it’s not uncommon for sellers on AliExpress to change the item they sell without changing the store listing, so even if you’ve purchased from a listing in the past, there’s no guarantee they will continue to offer the same items. This has happened to me with a seller I used previously and no longer recommend.

🔑  The motors that I’ve found work best for splitflap displays have a 64:1 gear ratio and a half-coil-resistance (measured from the red wire to the blue wire) of ~100 ohms.

----------

In my experience, I’ve found these tips improve your chances of getting good motors:

- 🔑 **Only buy motors labeled 12V**
    - It seems like there are more variants marketed as “5V” so you’re less likely to get a consistent item when buying 5V motors
- 🔑 **Only buy motors that have laser-engraved labels; avoid motors with sticker labels**
    - Laser-engraving is more expensive than stickers, so it generally suggests a higher quality product. I’ve received sticker motors with *identical* “serial” numbers printed on the sticker, whereas the numbers on laser-engraved motors have always been unique in my experience
- 🔑 **Message the seller beforehand to confirm the motors are as you expect**
    - Ask whether the motors have a sticker or laser-engraved numbers on the side 
    - You can try asking what the resistance is, e.g. between the red wire and blue wire, but I’ve had little luck with this in the past (maybe just lost in translation)
    - Asking about steps/rev or gear ratio is generally not useful; they will give you an answer but it may not be correct because they can’t easily test it

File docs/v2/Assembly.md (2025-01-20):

# Splitflap v2 Assembly Guide
[<< Back to Documentation Index](../DocumentationIndex.md)

# Electronics Part 1: Sensor PCBs

Start by removing the rails on the outside of the panel following the printed instructions, then snap apart the individual sensor boards.

Snap off the rails
Break apart the sensors

You’ll probably want to use some pliers to clean up the spacer segments that were between the sensor boards.




Then insert the right-angle headers from the side with the pins labeled (and where “MOTOR” is visible). The pin headers should extend down past the bottom of the PCB.



Flip the PCB and solder the headers in place.




# Electronics Part 2: Chainlink Driver & Chainlink Buddy [T-Display]
## Assemble the Chainlink Driver PCB

Insert and solder the connectors as shown. Note that both of the IDC connectors on the ends face the same way - notches facing left.



Insert the ribbon cable into a connector as shown, and *gently* clamp shut with a vise or pliers. Repeat with the other connector on the opposite end, making sure that both connectors face the **same** way - notches facing left.



(Not recommended, but you can optionally install the strain relief on the connectors: fold the ribbon cable back over the connector and install the plastic piece to clamp it down until it clicks. You’ll sacrifice some cable length and end up with a bulkier/taller connector, so I don’t think it’s worthwhile, especially since your cables shouldn’t be moving around much anyway.)

## Assemble the Chainlink Buddy

Solder the connectors into place (make sure the IDC connector notch faces the left, as indicated on the PCB)

**T-Display Buddy**




On the T-Display itself, you will solder the 2 rows of male headers (included in the box) to the T-Display, and then the whole module will plug into the matching female headers you soldered on the Buddy board.

You may notice a few empty spaces in the lower left of the T-Display Buddy PCB labeled C1 and C2 along with 3 through-holes; don’t worry, those are optional components for an advanced build and are not needed for a basic setup. 
See [Standalone T-Display operation](../ElectronicsGuide.md#8-optional-standalone-t-display-operation) for more info.



Note: the T-Display often comes with a small Red/Black wiring harness with connector as well; it cannot be used alongside the Chainlink Buddy and should be discarded.

**Breadboard Buddy (alternative to T-Display Buddy)**
If you’d prefer to use a different ESP32 module, you can use the Breadboard Buddy PCB to easily adapt the IDC cable to a breadboard.




## Connect Chainlink Driver to Chainlink Buddy

We’ll start by connecting and testing just the Chainlink Driver, without connecting a power supply or any modules’ motors or sensors. We’ll add those later, after confirming that the basic electronics work.

**T-Display**

- Connect the ribbon cable from the Chainlink Buddy’s **Output** to the Chainlink Driver’s **Input**
- Connect a wire from the Chainlink Driver’s “Logic 3.3-5V” screw terminal to the “3.3V” screw terminal on the Chainlink Buddy
- Connect a wire from the Chainlink Driver’s “GND” screw terminal to the “GND” screw terminal on the Chainlink Buddy
- Connect a wire from the Chainlink Driver’s “Motor 5-12v” screw terminal to the “12V” screw terminal on the Chainlink Buddy
- ⚠️  Never connect a battery to the T-Display’s battery connector (small white connector on the bottom of the TTGO T-Display module) when using the Chainlink Buddy! 


**Breadboard (if you’re not using the T-Display Buddy)**
If you are using a different ESP32 module with the Breadboard Buddy rather than the T-Display Buddy, see the instructions in the full [Chainlink User Guide](../ElectronicsGuide.md).

# Mechanical: Laser-cut Assembly


⚠️⚠️⚠️
If you used acrylic parts, DO NOT FORCE THEM together if they don’t fit immediately. The acrylic WILL shatter! Use a small jeweler’s file to shave down the parts as necessary. 
⚠️⚠️⚠️

## Flap drum

Take an M4x10 bolt and nut and loosely assemble them on the spacer piece. Make sure the bolt can still spin somewhat freely. Set this aside.



Hold the 4 struts to form a box, with the stepped tab ends facing up…



… and then place the spacer on top with bolt facing up/out.



Spin the bolt/nut combo to so the nut’s edges are parallel to 2 of the strut tabs, and then place the wheel with hexagonal center hole onto the end.



Then attach the other wheel to the other end’s tabs. You may need to hold the whole assembly together at this point if the laser-cut parts are a bit loose.



I recommend using CA glue (with accelerator!) to permanently assemble the flap drum. My personal go-to glue is Bob Smith Industries thick CA glue ([paid affiliate link](https://amzn.to/3REVhEM), or use this [non-affiliate link](https://a.co/d/05jtD1j4)). Note: make sure you’ve installed the M4 nut+bolt earlier, as you won’t be able to install it after gluing!

Apply a small dot of CA glue to each joint between the center struts and the wheel ends (8 dots in total). You will have 30 seconds to a minute of working time at this step.




If the assembly is somewhat loose, **make sure the wheel ends are not twisted**, as this will cause flaps to hang at an angle! See photo below for why this is problematic:

❌ AVOID TWISTING THE DRUM WHEN GLUING IT! ❌ Although you’re not installing flaps quite yet, a twisted drum will eventually look like this — flaps hang at an angle and may bind up against the sides of the front window!!!

When the drum is fully assembled and you’ve ensured it’s not twisted, spray CA accelerator to quickly lock the glue in place. If the parts are particularly loose, you may want to hold the assembly together with gloved hands while you spray CA accelerator.



💡 **Important CA glue tip:** If you don’t use accelerator, you’ll likely end up with a white haze or residue all over the acrylic parts — this is caused by small amounts of CA glue vaporizing and curing with the moisture in the air, which then gets deposited onto your parts (and surrounding table, computer, etc!) to make a permanent white-ish haze. I’ve never had issues with CA haze/fogging when using Bob Smith Industries glue with the included accelerator spray, which is why I recommend it! ([paid affiliate link](https://amzn.to/3REVhEM), or use this [non-affiliate link](https://a.co/d/05jtD1j4))

After waiting a few minutes for the accelerated CA glue to cure, use an allen key to tighten the internal M4 bolt and lock it in place.



## Motor + Sensor + Left enclosure

Take the wider of the side enclosure pieces (with a rounded rectangular hole cut out of the middle) and insert the motor’s cable through the hole in the orientation shown below.




Then place the sensor PCB over the motor, and insert 2 M4x10 bolts into the motor mount holes.




Flip the assembly over and start threading a nut onto each bolt, then use an allen key to finish tightening the nuts.






## Magnet

Next we’ll install the magnet into the flap drum. The orientation of the magnet is critical, as the sensor only works with one pole of the magnet and not the other!

Luckily we can use the LED on the sensor PCB to help determine the right way to install the magnet.

Plug the sensor into your Chainlink Driver, and connect the Chainlink Driver to your ESP32/Chainlink Buddy, ensuring you’ve connected the 3.3v logic power screw terminals. 



When you hold up the magnet, the LED should light for one side of the magnet and not the other.

The LED on the sensor PCB will light when the magnet is in the correct orientation
This is the wrong orientation - the LED is not lit

Install the magnet into the flap drum in the orientation that caused the LED to light.

I’ve found that attaching the magnet to one jaw of a set of pliers and then **gently** pressing it into the flap drum works well — DO NOT FORCE IT if it requires more than a tiny bit of pressure, as you will crack the acylic; use a file to widen the hole and then try again.

Magnet stuck to pliers in correct orientation
Gently pressing until flush

Installed magnet

Double-check you got the magnet orientation correct when installing the flap drum onto the motor. Again, it should gently press-fit onto the motor shaft; use a file to widen the hole first if it requires too much force to press into place.



If the magnet is a little loose, you can add a drop of CA glue on the back side (from the inside of the drum) to lock it in place.

## Top/Bottom/Right Enclosure Pieces

The top and bottom pieces are interchangeable with each other. Find the matching tabs and slots of the top piece and the left side (with the motor)…



… insert a nut into the notch in the top piece (I like to support it from behind with a finger as shown below) and screw in an M4x10 bolt to connect the pieces.



Repeat that process with the bottom piece, and then attach the right side piece as well.

Place the backstop bolt in the center of its slot to start

Before installing the front face, insert the M4x10 flap backstop bolt in the middle of the slot on the right side piece and secure in place with a nut. You can fine-tune the position later if desired, but the middle is usually a good starting point.

Flap backstop bolt sticks in towards the middle of the module

Now attach the front face using M4 bolts/nuts to secure it to the top and bottom pieces.



## Installing flaps

Now you can install the flaps. The first flap you install should be blank and the bottom half of the letter “A”.



Install the first flap into the position shown below — 90 degrees “ahead” of the magnet on the flap drum. (this position technically isn’t critical since the home position is software-calibrated later, but it’s a nice convention to keep the modules consistent with each other)



Gently bend the flap to insert it

To install a flap, let it rest between your index and middle fingers, and press on the middle with your thumb to bend the flap. Insert one of the flap’s pins into the flap drum, then carefully align the other pin and gently release pressure from your thumb to insert the second pin as the flap unbends.

Repeat with the next 51 flaps, making sure to confirm the ordering as you do so.



# Firmware
- Download and install [Microsoft Visual Studio Code](https://code.visualstudio.com/)
- Follow these steps to set up Platform IO and the splitflap code:
    - Install the Platform IO extension
    - Choose “Clone Respository” in the Explorer sidebar and enter the git repo URL: `https://github.com/scottbez1/splitflap.git`
    - Once it's done cloning, select the option to open it
    - You may need to choose to “Trust” the folder to allow the Platform IO extension to run.

You’ll need to configure NUM_MODULES in `platformio.ini` to match the number of modules supported by the Chainlink Drivers you have connected. So for a single Chainlink Driver, set it to 6.

    [env:chainlink]
    extends=esp32base
    build_flags =
        ${esp32base.build_flags}
        -DCHAINLINK
        -DNUM_MODULES=6

- Mac Users: you will likely need to install updated drivers for the CH9102 USB-serial adapter used on newer versions of the ESP32 T-Display: https://learn.adafruit.com/how-to-install-drivers-for-wch-usb-to-serial-chips-ch9102f-ch9102/mac-driver-installation
- To upload code to the ESP32 T-Display from VS Code, you’ll need to (see screenshot below):
> 1) Open the Platform IO sidebar (click the alien icon on the left)
> 2) Click the “env” button at the bottom of the window and then in the dropdown at the top of the screen…
> 3) …select “env:chainlink” as the environment - this will set up code completion and syntax highlighting for the ESP32
> 4) in the  Platform IO sidebar, expand the “General” section, and click `Upload and Monitor` 


- If you reset the ESP32, you should see the LEDs on the Chainlink Drivers blink quickly and a message in the serial monitor that loopbacks are ok. If you see a loopback error message, troubleshoot that before continuing.

## Connect modules and power

**Motors**

- Plug into the white connectors. Note that module connections are laid out from *right-to-left* since the Chainlink Driver PCB is intended to sit *behind* the modules, so the first module plugs into position “A” on the **right** side of the PCB

**Sensors**



- Plug sensor cable into corresponding 3-pin header
- Ground (black) should be on the left, labeled “-”
- Signal (usually white or yellow) should be on the right (toward the “Input” side), labeled “S”
## 

**Power**
The ESP32 and 3.3v electronics on the Chainlink Drivers are typically powered by the USB connection to a computer. 12V power for the motors is supplied via a separate power supply.

> Note: avoid turning on 12V power when the ESP32 is not running! Doing so could damage your motors or worse, as the motor coils could be "stuck on" if the ESP32 is not running.

**T-Display**

- You can plug a DC 12v barrel jack into the T-Display Buddy when using 1 or 2 Chainlink Drivers for up to 12 modules.
- ⚠️ For more than 2 Chainlink Drivers, the barrel jack **cannot handle enough current**, so you should instead connect your power supply directly to the Motor Power terminals of the first Chainlink Driver.
Make sure you are using the [appropriate wire gauge](../ElectronicsGuide.md#power-supply-tips), and [never chain power to more than 6 Chainlink Drivers](../ElectronicsGuide.md#large-displays)
https://www.dropbox.com/s/4xpvtycwrw21g0e/chainlinkBuddyWiringv1.1.pdf?dl=0

**Breadboard**

- Connect your power supply directly to the Motor Power terminals of the first Chainlink Driver. Make sure you are using the [appropriate wire gauge](../ElectronicsGuide.md#power-supply-tips), and [never chain power to more than 6 Chainlink Drivers](../ElectronicsGuide.md#large-displays)

For further wiring info, see the full [Chainlink User Guide](../ElectronicsGuide.md).

# Initial Setup & Calibration
- Turn on your 12V supply and plug the ESP32 into your computer.
- You should see the modules start to find their home positions.
    - If none of modules move, try restarting the ESP32. If they still don’t move, turn off your 12V supply and see the [troubleshooting section](#troubleshooting)
- In Chrome or Edge (unfortunately Firefox will not work, as of 2024-10-05), go to https://scottbez1.github.io/splitflap/ and connect to your display via Web Serial
- If a module is showing as an orange square, you should first try re-homing the module by left-clicking it. You should see the module spin and find its home position. If this does not resolve the sensor error, see the [troubleshooting section](#troubleshooting)
- Right-click a module to open the calibration flow, and follow the instructions to complete calibration. Save the calibration before continuing to calibrate the other modules.
    - If saving the calibration fails, see the [troubleshooting section](#troubleshooting)

https://www.dropbox.com/scl/fi/aqilx2zk5q8ic1kwi2ki7/PXL_20240330_182017129.TS.mp4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

# Troubleshooting
- Modules don’t move at all when the ESP32 and 12V supply are turned on
    - Troubleshooting steps:
        - Run the “Monitor” PlatformIO action in VSCode and then press the reset button on the ESP32. You want to see a message like `{"type":"init", "num_modules":6}` and not any messages about loopback errors (see section below if you do see a `Loopback ERROR`)
        - Make sure your screw terminals are securely clamped onto the appropriate wires
        - Use a voltmeter to confirm that there is 11-13V measured between the Motor and GND screw terminals on each Chainlink Driver board
- Saving module calibration fails
    - Symptoms: `Failed to open config file` or `Failed to mount FFat` messages when saving calibration
    - Troubleshooting steps:
        - In VSCode, use the PlatformIO action to erase the flash on your ESP32, then re-upload the firmware and try calibration again
- Bad chainlink data signal - `Loopback ERROR`
    - Symptoms: `Loopback ERROR` log message. This means the control signals to the motors or from the sensors are not working along the chain of Chainlink Driver boards.
    - Troubleshooting steps:
        - Check all of your solder joints, especially those on the IDC connectors, to make sure they are solid and not bridged
        - Make sure the IDC ribbon cable connectors are fully clamped onto the ribbon cables
        - Check all of the screw terminals are securely clamped onto the appropriate wires
        - Make sure the NUM_MODULES variable in platformio.ini (under the `env:chainlink` section) is set to 6 times the number of Chainlink Drivers you have connected
        - Press the reset button on the ESP32 and confirm that the red LEDs on the Chainlink Drivers each flash sequentially once

if you have questions not covered here, please reach out in the [splitflap Discord server](#troubleshootings).

----------

Link disclosure: As an Amazon Associate I earn from qualifying purchases at no cost to you.
(I’ve also chosen to include non-affiliate links next to every affiliate link should you prefer to avoid using affiliate links)

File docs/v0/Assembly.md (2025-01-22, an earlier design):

# Splitflap v0 Assembly Guide
[<< Back to Documentation Index](../DocumentationIndex.md)

## Intro
Building a split-flap display? I would love to hear from you and see photos/videos of your project in progress or completed! This project has been a hobby of mine for a few years and the coolest part by far is hearing from other people making their own and seeing them in action. Feel free to shoot me an email at scott@bezeklabs.com 🙂 or, [join the Discord server](https://discord.gg/wgehm3PcrC) to share and discuss with the wider split-flap community!

# 1. Gather the parts

See the [complete ordering guide (v0)](OrderingComplete.md) or the [easy guide (v0)](OrderingEasy.md) for info on ordering parts

- 1 Controller PCB
- 4 Sensor PCBs
- 4 Magnets
- components for controller and sensor boards

&nbsp;

- 4 laser-cut panels
- 2 letter sticker packs
- 4 motors
- 4 sensor cables
- ~165 flaps (160 are necessary)
- ~46 M4 bolts (44 are necessary)
- ~46 M4 nuts (44 are necessary)

&nbsp;

- 12V 2A Power Supply
- Tools:
    - Metric hex key
    - Soldering supplies
    - Calipers or metric ruler
    - Hobby knife
    - Plastic wrap and glass storage container (For applying letter stickers)
    - [if hand-cutting flaps] Badge slot punch 
# 2. Sensor PCB Assembly
https://www.youtube.com/watch?v=vQMnWK6PwJ0&

> 💡 **New (not shown in video!):** The laser cut files include a jig for spacing the hall effect sensor accurately without having to measure the 5.8mm gap. See photos of it below.
>  
> The latest PCB design also has holes that are spaced further apart for the sensor to make soldering them easier. You’ll need to bend the sensor’s pins outward to fit into the holes.

The rough steps are:

- solder 90-degree pin headers *from the top side* ([0:21](https://www.youtube.com/watch?v=vQMnWK6PwJ0&t=21s))
- bend leads on hall effect sensor 90 degrees ([2:00](https://www.youtube.com/watch?v=vQMnWK6PwJ0&t=120s))
- insert hall effect sensor from the back side of the PCB (opposite the pin headers) ([2:45](https://www.youtube.com/watch?v=vQMnWK6PwJ0&t=165s))
- adjust hall effect sensor so there's a ~5.8mm gap between the back of the sensor and the PCB ([3:00](https://www.youtube.com/watch?v=vQMnWK6PwJ0&t=180s))
- solder the hall effect sensor in place ([3:30](https://www.youtube.com/watch?v=vQMnWK6PwJ0&t=210s))
- clip off excess pin length ([4:24](https://www.youtube.com/watch?v=vQMnWK6PwJ0&t=264s))

<a href="https://paper-attachments.dropbox.com/s_DBFFE29691B90C2EDDE2A687CA2E739A14BF58F2DE09EF37D4E0562373661460_1643174894237_123306848-a4ecbc00-d4d6-11eb-9b46-d47165f3abe7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">
    
</a>
<a href="https://paper-attachments.dropbox.com/s_DBFFE29691B90C2EDDE2A687CA2E739A14BF58F2DE09EF37D4E0562373661460_1643174893952_123306852-a6b67f80-d4d6-11eb-9466-73a11368e9a7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">
    
</a>

> Sensor spacing jig cut from white acrylic

<a href="https://paper-attachments.dropbox.com/s_DBFFE29691B90C2EDDE2A687CA2E739A14BF58F2DE09EF37D4E0562373661460_1643174982515_123307566-7de2ba00-d4d7-11eb-8d17-976c0b2a1335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">
    
</a>

> If your laser cut parts came in a full sheet as-cut (e.g. Ponoko does this, but not Elecrow), you’ll find the jig inside the motor cutout, highlighted in red above

# 3. Mechanical Assembly

Note: if using acrylic rather than MDF/wood, *do not force parts together* if they don’t quite fit. Acrylic is extremely brittle and *will* crack. Use a small file if necessary to remove any excess material. While the design attempts to achieve a tight fit, different laser-cutters may remove more or less material, so undersized holes/slots can occur.

https://www.youtube.com/watch?v=zHM8W6Rm2i4&

The rough steps are:

- separate laser-cut parts ([0:12](https://www.youtube.com/watch?v=zHM8W6Rm2i4&t=12s))
- remove protective film ([0:34](https://www.youtube.com/watch?v=zHM8W6Rm2i4&t=34s))
- Spool:
    - put together spool struts ([1:31](https://www.youtube.com/watch?v=zHM8W6Rm2i4&t=91s))
    - attach bolt+nut to spool retaining piece ([2:16](https://www.youtube.com/watch?v=zHM8W6Rm2i4&t=136s))
    - insert spool struts into spool disk ([2:50](https://www.youtube.com/watch?v=zHM8W6Rm2i4&t=170s))
    - press other spool disk onto spool struts ([3:25](https://www.youtube.com/watch?v=zHM8W6Rm2i4&t=205s))
    - check magnet polarity and insert magnet into spool ([3:40](https://www.youtube.com/watch?v=zHM8W6Rm2i4&t=220s))
- pass motor through side hole and secure with 2 bolts ([5:05](https://www.youtube.com/watch?v=zHM8W6Rm2i4&t=305s))
- mount hall effect sensor module and secure with a bolt ([6:02](https://www.youtube.com/watch?v=zHM8W6Rm2i4&t=362s))
- press spool onto motor shaft ([7:15](https://www.youtube.com/watch?v=zHM8W6Rm2i4&t=435s))
- press fit bottom piece into left piece, with laser-engraved lettering facing up and circular hole toward the back ([7:50](https://www.youtube.com/watch?v=zHM8W6Rm2i4&t=470s))
- press fit top piece into left piece, with circular hole toward the back ([8:14](https://www.youtube.com/watch?v=zHM8W6Rm2i4&t=494s))
- press right piece into top/bottom pieces and aligned with spool axle ([8:34](https://www.youtube.com/watch?v=zHM8W6Rm2i4&t=514s))
- press front piece into top/bottom pieces, with thicker side on the left ([9:05](https://www.youtube.com/watch?v=zHM8W6Rm2i4&t=545s))
- secure enclosure pieces using captive nuts+bolts ([9:27](https://www.youtube.com/watch?v=zHM8W6Rm2i4&t=567s))
- attach flap backstop bolt/nut ([10:26](https://www.youtube.com/watch?v=zHM8W6Rm2i4&t=626s))
- to connect to another module, remove front face, insert inter-module connectors, and replace front face ([10:55](https://www.youtube.com/watch?v=zHM8W6Rm2i4&t=655s))
# 4. Applying Letter Stickers
https://www.youtube.com/watch?v=3lFECISLwyI&

## Additional notes (not in the video above):

By default, the splitflap code assumes the flaps appear in a particular order, so it’s easiest to apply the stickers as follows:

    (space), A, B, C, D, E, F, G, H, I, J, K, L, M, N, O, P, Q, R, S, T, U, V, W, X, Y, Z, 0, 1, 2, 3, 4, 5, 6, 7, 8, 9, (period), (comma), (apostrophe)

Note: for a display that will commonly count *down,* it may make sense to reverse the order of the numbers so that counting down doesn't require a full revolution each time.

You will need to make a few simple changes to the control software to tell it what order the letters appear if you use something other than the default.

Do not insert the flaps into the spool until step 6 (just keep them in order).

# 5. Electronics Assembly

See the [Electronics Guide](../ElectronicsGuide.md) for complete instructions on assembling and using the electronics.

# 6. Final Assembly and Calibration

Rough steps:

- Setup
    - Download and install [Microsoft Visual Studio Code](https://code.visualstudio.com/)
    - Follow these steps to set up Platform IO and the splitflap code ([watch](https://youtu.be/uyG5mEKzKcg) [screencast](https://www.youtube.com/watch?v=C8mcExG-VVo)):
        - Install the Platform IO extension
        - Choose “Clone Respository” in the Explorer sidebar and enter the git repo URL: `https://github.com/scottbez1/splitflap.git`
            - Note: downloading the source as a zip from github is **NOT recommended**, as it will make it harder to get help if any issues arise (git will keep track of which precise version of the code you checked out, along with any changes you make, which helps a lot when debugging)
        - Open the repository. You may need to choose to “Trust” the folder to allow the Platform IO extension to run.
        - Install the splitflap firmware on the device and open a serial monitor
            - Open the Platform IO sidebar and run the `chainlink` → `Upload and Monitor` task
- Confirm that you see the startup message that looks like this:
    {"type":"init", "num_modules":12, "character_list":" abcdefghijklmnopqrstuvwxyz0123456789.,'"}
- Plug in all motors and sensors
- Plug in 12V motor power
- Restart the microcontroller
    - Spools should rotate slowly until the home position is reached, then complete one revolution at full speed
    - Make sure spools are rotating the right direction
    - Confirm that all 4 RGB LEDs are green before moving on
- Open Serial Monitor - we’ll do some testing to make sure the motors are configured correctly
    - Send `=    \n` (equal space space space space newline)
    - Check that all motors complete a full revolution and stop
    - Repeat this process 10 more times and make sure that none of the modules have to recalibrate (rotate slowly as in the startup procedure) during this test
    - Confirm that the reported `"count_missed_home":0, "count_unexpected_home":0` values are both zero for all 4 modules
- Send `@` in Serial Monitor to force all modules to recalibrate, and `=    \n` to tell all the modules to go to the home position
- Install flaps

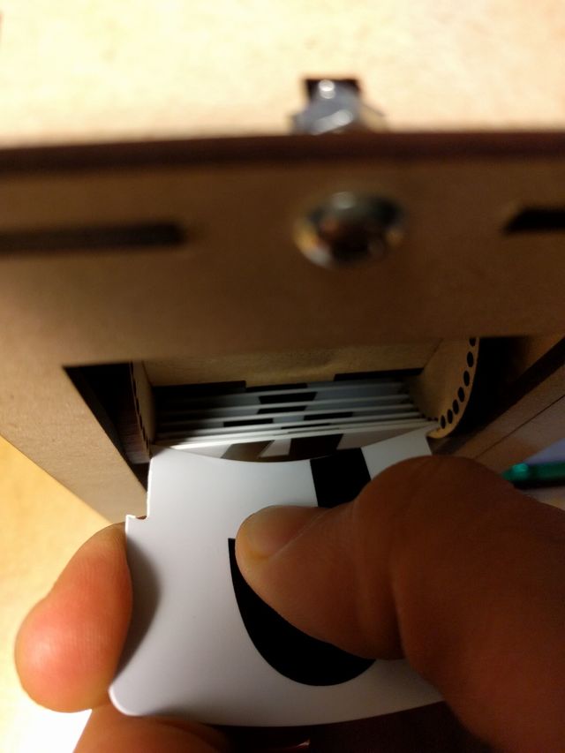
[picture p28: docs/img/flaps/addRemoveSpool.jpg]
Gently bend the flap with your thumb to add or remove it
  

    - Start by taking the top and bottom halves of the empty (space) character. Insert the top half into the holes marked with a “-” on the spool. Insert the bottom half into the spool holes below it. 
    - Rotate the spool forward a few characters (e.g. by sending `=e\n` or by gently rotating the spool by hand) and insert the next few flaps. Repeat this until all 40 flaps are installed.
- Calibration
    -  Use the Serial Monitor to send characters to the modules 
    - If the module consistently doesn’t turn quite far enough or turns a little too far for some letters, then the home position sensor may need to be adjusted:
        - Loosen the hall-effect sensor bolt
        - If the module wasn’t turning far enough, slide the sensor toward the **rear** of the module
        - If the module was turning a little too far, slide the sensor toward the **front** of the module
        - Re-tighten the hall-effect sensor bolt
        - Send a `@` to recalibrate
        - Check if the calibration is better now

# Legacy Classic Controller Assembly

https://www.youtube.com/watch?v=VmKuWdmhPtM&&feature=youtu.be

Components with polarity have been labeled with a ⚠️  symbol below - make sure you get the orientation correct!

Recommended assembly order:

- 4 WS2812b RGB LEDs - U5, U6, U7, U8 - center near A B C D labels
    - ⚠️ Make sure to get polarity correct - LED notch aligns with right-angle silkscreen line - top left corner (on some PCBs, this marker may be missing or hard to see; just make sure the notch is pointing toward the top left corner)
- Arduino pin headers (BOTTOM SIDE):
    - 3 pin straight male header - “Arduino D4 D5 D6” label on bottom
    - 2x3 Female header - ISP label on bottom
    - 2 pin straight male header - VIN label on bottom
- 470 resistor (Yellow Purple Brown) - R9 (center top side, between the two MIC5842 spots)
- Top left corner:
    -  2 pin straight male header - JP1
    - **Yellow** LED - D1 (Mot+) - ⚠️ make sure to get polarity correct - match flat side to silkscreen
    - **Green** LED - D2 (5V)- ⚠️ make sure to get polarity correct - match flat side to silkscreen
    - 2.2k resistor (Red Red Red) - R1
    - 220 resistor (Red Red Brown) - R7
- Capacitors:
    - 100uF electrolytic capacitor - C1 - ⚠️ make sure to get polarity correct
    - 100uF electrolytic capacitor - C3 - ⚠️ make sure to get polarity correct
    - 0.1uF capacitor - C2 (to the left of “A” LED)
- Barrel Jack Connector - top right “5-12V” label
- Sensor connectors (place all of these at once with a sensor cable plugged in across all 3 to ensure proper alignment when soldering)
    - 4 pin straight male header - “GND” label
    - 4 pin straight male header - “5V” label
    - 4 pin straight male header - “A” and “D” labels
- 47k resistors (Yellow Purple Orange) - R3 R4 R5 R6 R10
- Motor connectors - P1 P2 P3 P4 - ⚠️ make sure to get polarity correct (match silkscreen)
- ICs - make absolutely sure to get the polarity correct!!!!
    - MIC5842 - U2 - ⚠️ make sure to get polarity correct (match silkscreen - notch facing **left**)
    - MIC5842 - U4 - ⚠️ make sure to get polarity correct (match silkscreen - notch facing **left**)
    - 74HC165 - U3 - ⚠️ make sure to get polarity correct (notch facing **bottom** - see right-angle silkscreen line near pin 1)

Assembled Driver PCB with optional EXP OUT connector (EXP OUT is only needed when chaining controllers to support more than 4 modules, see below for more details)

You should have the following parts left over:

- Jumper connector - this is an optional component that is generally not needed; you should leave it off unless you're certain you need it. **Never connect the Arduino's USB cable to anything if jumper JP1 is in place!** The JP1  to power the Arduino from the driver board’s motor power supply, allowing the Arduino to run without a computer connection.  - while the Arduino theoretically protects against 12V back-flowing to the USB connector via the VIN pin, you risk damaging your computer if that protection fails (or is not implemented for some reason on a cheap knock-off Arduino clone).

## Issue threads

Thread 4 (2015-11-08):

Press-fit holes are slightly too small

scottbez1, 2015-11-08:
The press fit holes for the 5mm rod and motor shaft are slightly too small.

Closed 2015-11-15.

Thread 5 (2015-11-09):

Add lower flap backstop

scottbez1, 2015-11-09:
Should add a backstop to prevent the lower flaps from swinging past 180 degrees - this prevents the swinging motion and helps get a louder "flap" noise. Currently using a roll of pennies (19.2mm diameter) resting on the bottom, with the center of the roll ~61 mm forward from the back wall.

Can make this with a perpendicular piece held in place with a bolt/captive nut coming up from the bottom, and tabs with extra long slots so that it can be adjusted forward/backward.

scottbez1, 2015-11-17:
Might be easier/cheaper to just cut a slot in the right side wall for an M4 bolt to stick inward and act as a backstop (adjustable horizontal position within the slot)?

The standard 12mm bolts are just long enough to retain flaps.
Would also need to cut a hole/slot in the left side wall for the adjacent bolt head.
Could potentially stick some shrink tubing over the exposed threads to reduce wear on the flaps.

Closed 2015-11-28.

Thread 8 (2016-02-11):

cards

raoul170, 2016-02-11:
the widest point on the "tab" is 1.5 mm correct?  Can it be square?  Can the "hight" (15mm) be lower?
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

scottbez1, 2016-02-11:
The thickness of the tab is mostly determined by `flap_hole_radius` in `splitflap.scad`, which is [currently 1.2mm](https://github.com/scottbez1/splitflap/blob/7ef2539ad5551fa2707af5be54aa41065ebd93ef/3d/splitflap.scad#L94).

That gives a theoretical max tab thickness of 2.4mm, but of course it needs to be smaller because the cards have some thickness and you want them to be able to rotate easily within the 2.4mm hole. In practice the cards that I've made have a tab thickness that measures somewhere between 1.2 and 1.6mm.

Square edges would work just fine, and in fact I'd prefer those but couldn't come up with a cheap/easy way to fabricate cards with square edges - would love to hear if you have suggestions there! Note that after using the slot punch on the cards I used diagonal cutters to snip off the sharp points left over to make the holes slightly more square - see the last 2 photos here: https://github.com/scottbez1/splitflap/wiki/Cut-flaps

The necessary height of the cutout is slightly tricky. It's important that it's a certain minimum size to allow the flap to swing all the way tangent to the spool (giving the flap a full 180 degrees of rotation):
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

That value is a little annoying to calculate by hand, so `splitflap.scad` does a [rough calculation based on the input parameters](https://github.com/scottbez1/splitflap/blob/c2433e25229c66a62a86a215dc629cc6730d6cef/3d/splitflap.scad#L120) and prints it out during rendering:
```
ECHO: flap_notch = 10.4717
```
That's likely going to be on the lower bound of what's necessary though; empirically I'd guess anything less than 12mm might start causing issues, and the 15mm from the punch gives plenty of margin.

raoul170, 2016-02-11:
I am concidering to produce 500 sets (20k flaps) with card manufacture. Printed white letters on black "card"   They need to make some stamp mould for it.

Any Ideaa what font used on the Vinyl stickers?  Cannot find such narrow/high font for now anywhere. "Gothic black" seems not correct.   The "robo" font in seems also too wide.

scottbez1, 2016-02-11:
500 sets?!? Wow, that's some impressive volume! At that scale I'm not sure
how helpful my advice will be considering I've only built 2 prototype units
so far, but I'd love to hear how your project goes!

Also depending on your plans and whether you're looking to build full units
based off the designs here, I feel like I should caution you that
everything in this repo is very much under active development -- e.g. in
order to get the IR reflectance sensor to work well, it's very likely I'll
need to add another laser cut hole to one of the spool pieces soon, but
that's not currently reflected in the 3d model.

As for the font, there is a small discussion of the "correct" typeface
originally used on Solari boards here: (sorry for the archive link, I can't
seem to find the info on their current site any more)
http://web.archive.org/web/20150802041313/http://beachlab.org/flip-flap

I favored low cost in small quantities over authenticity though, and just
went with whatever font I could find with appropriately sized stickers :-P
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

Closed 2016-02-17.

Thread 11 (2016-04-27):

Investigate JTAG pin state interaction with optical sensors

scottbez1, 2016-04-27:
The sensor input pins are on Port F, bits 4, 5, 6,7; however, by default JTAG is enabled, and according to the datasheet:

> Port F also serves the functions of the JTAG interface. If the JTAG interface is enabled, the pull-up resistors on pins PF7(TDI), PF5(TMS), and PF4(TCK) will be activated even if a reset occurs

This seems mostly fine, as we can disable the JTAG mode at runtime using

```
  MCUCR |= (1<<JTD);
  MCUCR |= (1<<JTD);
```

However, experimentally it seemed like PF6 was also at 5V at startup, which is the TDO (JTAG Test Data Output) pin. If during reset this pin is driven high as an output (unlike the other JTAG pins which should be configured as inputs with the internal pull-ups enabled), this could prove disastrous for the GP2S60, which has a maximum collector current of 20mA whereas the ATmega32U4 can source up to 40mA. Two possible fixes are either to change the JTAGEN fuse (requires ISP header pins and a programmer which adds a lot of complexity) or modify the pcb to add a series resistor between the GP2S60 collector and PF6 to limit the maximum current if the pin is set as a high output during reset.

scottbez1, 2016-04-27:
Also noticed this specific mention of TDO:
>The TDO pin is tri-stated unless TAP states that shift out data are entered.

Presumably there is no "shift out data entered" in the initial Test-Logic-Reset state, but then it seems odd that the pin would have the internal pull-up enabled while in high-impedance mode without also mentioning that in the datasheet.

scottbez1, 2016-04-28:
With some more reading it sounds like TDO should be in high impedance mode by default. I guess if the board is not running the main code that disabled JTAG (e.g. while the dfu bootloader is active) it is possible you'd get unlucky and trigger TAP state transitions via the optical sensor inputs and end up enabling TDO as an active output and wreck the GP2S60 though...

Another fix that might work is to avoid using TDI/TDO pins entirely (or maybe TDI and TMS are the ones to avoid?) and use PF0 and PF1 (or even PE6) instead in a future PCB rev.

Closed 2018-02-08.

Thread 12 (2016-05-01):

Electronics/PCB should be more approachable to build

scottbez1, 2016-05-01:
Unfortunately the current PCB design is a little tricky for a beginner hobbyist to assemble due to the surface mount TQFP ATmega32U4 and micro USB connector which take some practice and patience to solder (the resistor pack is also tricky to solder, but that could easily be replaced by individual 0805s).

It might be interesting to design a variant that uses an Arduino Micro instead, with only through-hole parts. It would be more expensive but would make the electronics more approachable (Micro costs ~$25, minus the ~$8 you save by not purchasing the chip and peripherals standalone: resistors, capacitors, usb port, crystal, etc). I suspect it'd still be possible to fit within the 50x50mm desired size for low cost PCB production.

scottbez1, 2016-06-13:
It's also tempting to consider an Arduino Uno shield, since Uno's are ubiquitous, but with the current driver design an Uno can only support 3 modules: each module needs 4 stepper pins + 1 sensor pin, but the Uno only has 18 IO pins available since Rx/Tx are needed for USB serial.

So there are a number of different approaches to consider with different tradeoffs:

| Option | MCU | Driver | Supported Modules | Requires SMD soldering | Notes |
| --- | --- | --- | --- | --- | --- |
| 1 | ATMega32U4** | 3x ULN2003A | 4 | Yes | Original design |
| 2 | Arduino Uno (shield) | 2x ULN2003A | 3* | No | Limited to 3 modules by IO pins |
| 3 | Arduino Uno (shield) | 2-4x MIC5842 | 4-8?* | No | Need to research MIC5841 more. |
| 4 | Arduino Micro (plug in) | 3x ULN2003A | 4* | No | Arduino Micro board isn't common, easily confused with Pro Micro, etc |
| 5 | Arduino Uno (shield) | 1-2x MC33996 | 4-8?* | Yes | Potentially enables driving more modules, but need to research MC33996 more |

\* Supported module count is a guess; might be lower depending on PCB size (50x50mm) constraint.
\*\* It looks like this could be downgraded to a U2 series 32-pin AVR for potential cost savings and smaller footprint; using PB0-7, PC4-7, PD0-7, with PC2 spare (e.g. single debug led).

One other related area for exploration is the possibility of stackable shields or expansion boards to support additional modules. With serial/shift-register outputs like the MIC5842 or MC33996, and potentially shift-register inputs for sensors, it seems theoretically possible to support more modules from a single microcontroller, though I haven't given too much thought to the serial data rate needed to drive the steppers.

scottbez1, 2017-03-24:
For prototyping I ended up ordering the MIC5891 rather than the MIC5842, partly by accident, but it's also ~$0.80 cheaper in single quantities at DigiKey -- $2.04 each in a DIP package. The MIC5891 is a high-side driver as opposed to the MIC5842 (or existing ULN2003A) but either should work fine as far as I know.

Updating the stepper driver code to use SPI for shifting out data (as opposed to direct port manipulation) was pretty straightforward and seemed to work just as well.

Overall this seems like the way forward for the electronics: the board can now just be an Arduino shield that's entirely through-hole soldering, which should make it way more approachable for hobbyists than the SMT soldering and DFU programming needed with the current design. Using a shift-register driver also allows the driver boards/shields to be easily chained to drive even more splitflap modules from a single microcontroller.

And assuming we also use shift-registers for the sensor inputs, the "shield" should only need to connect to the ICSP header on the Arduino which connect to the high speed SPI pins regardless of specific Arduino model.

scottbez1, 2017-09-30:
Work is ongoing in the [shift_register branch](https://github.com/scottbez1/splitflap/tree/shift_register) on this new shift-register based design.

Arduino code has been updated to support driving chained MIC5842 shift register outputs and uses SN74HC165 shift registers for sensor inputs.

The plan is for a single Arduino Uno to be able to drive up to 12 character modules, via 3 chained electronics boards. Each PCB would have 2 MIC5842 output registers for driving 4 stepper motors and 1 SN74HC165 for reading the sensor inputs, and ideally will be entirely through-hole soldering for ease of construction.

The new design has been tested with 3 modules, with prototype breadboard electronics. Work on an updated PCB design will begin soon.

whitebird, 2019-02-01:
One method you can use to simplify design is to allow place for a generic Arduino Micro board. That way you don't have to solder the micro usb port and atmega32u4.

Closed 2018-02-08.

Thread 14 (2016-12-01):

incorrect rod size

fpagliar, 2016-12-01:
I see the materials list includes:
 5mmx100mm rod
but judging on the pieces I got from Ponoko, it seems like it should be 4.5mmx100mm.
Is this the case?

scottbez1, 2016-12-01:
Hey, sorry I need to improve the documentation a bit! The latest design on the tip of master is actually an experimental one, that replaces the 5mm rod with 2 M4 bolts facing inward from the sides, which is different than what's shown in the wiki. I haven't actually tested this design yet, but it sounds like you've ordered this latest design from Ponoko, so let's see if it works!

The idea is that each of the sides have an M4 bolt facing inward, with a nut on the inside to hold it in place. (Those nuts takes the place of the bushings that used to be there as mentioned in #15). So I think you want to attach those bolts to the left/right sides, and then put all but one side of the enclosure together, slide the spool onto the bolt and hold it in place while you slide on the last enclosure side, lining up its bolt with the hole on the other side of the spool as you do so.

Hopefully that makes sense? Wish I had some photos I could share, but maybe you could take some to help improve the wiki if this design works out as planned?

Thanks! Let me know if you run into any problems!

fpagliar, 2016-12-02:
Great, I'll try it out, thanks!

fpagliar, 2016-12-05:
Great! It works correctly.
Thanks!

scottbez1, 2016-12-08:
Awesome! Glad to hear it. I'd love to hear how the rest of your build turns out!

Closed 2016-12-05.

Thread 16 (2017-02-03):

Numbers only

samer-riad, 2017-02-03:
Hey Scott,
I was wondering if I wanted to make it numbers based only. No characters. How would this affect the code and the size of the wheel hosting the cards and the entire mechanism?
Cheers,
Sam

scottbez1, 2017-03-07:
Hey Sam, sorry for taking sooooo long to respond! I haven't looked too much into making a number-only display, but here are some thoughts from playing around with it for a few minutes:

You can easily decrease the number of flaps by adjusting the [num_flaps variable](https://github.com/scottbez1/splitflap/blob/f1d1edbba32aee4835e0c66f7c48eed6c3641932/3d/splitflap.scad#L95), but this reveals some other issues:

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

(In this example I decreased the number of flaps to 10, though you would maybe want to include at least one more so there can be an empty flap in addition to numbers 0-9)

The things you see sticking out of the center there are the "spool struts" which make sure that the disks on either side of the spool turn at the same speed. On the 40 flap design, those struts fit into rectangular holes in the disks and hold the spool in alignment:

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

But when the spool disks are much smaller for just 10 flaps, there isn't enough room for those struts in the center of the spool any more, so some modification would probably need to be made, such as replacing the fixed axle with a rotating axle, where each side of the spool is glued or attached to the axle to keep them aligned. Depending on materials and desired longevity, you would maybe want to add bearings on the enclosure to allow the axle to spin with less friction.

If we set aside the struts and look at the other side, the gear appears to be sticking out of the front:
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

We can change the size of that gear by adjusting the [spool_teeth variable](https://github.com/scottbez1/splitflap/blob/f1d1edbba32aee4835e0c66f7c48eed6c3641932/3d/splitflap.scad#L105) and shrink it down to something like 10 teeth:
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

However, now the motor has a gear with 40 teeth and the spool has 10 teeth, meaning the spool will spin 4 times for every revolution of the motor! The motor may not have enough torque for that, and such a high gear ratio also reduces the precision available from the stepper motor. So it would probably make sense to also decrease the [motor_teeth variable](https://github.com/scottbez1/splitflap/blob/f1d1edbba32aee4835e0c66f7c48eed6c3641932/3d/splitflap.scad#L103).

This of course introduces a new minor problem - with the smaller gears, the motor ends up much closer to the flaps. This is fine for a single display, but if you were to place 2 next to each other, the flaps of one display would hit the motor from the adjacent display:
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

One solution to that is to increase the size of the idler gear, which doesn't affect the gear ratio at all:
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

At this point the design is getting pretty close to something that could work, though there are a few more details that would need to be worked out (home position sensor/pcb mounting holes, bushing sizes, etc). I'd encourage you to check out the OpenSCAD code and play around with changing different variables and seeing what happens! I'm sure there are tons of variations and possibilities I haven't even considered yet, and I'd love to hear what you come up with.

DurandA, 2017-06-14:
Thank you for the *very* detailed answer. I'm also interested in building an Internet-connected counter out of it!

bobc, 2018-02-21:
I'm also interested in a numbers only display for a clock.

One workaround for the mechanical issues might be to repeat each digit several times, so 4 times 10 gives 40. Then you need to adjust the control circuit to advance 4 flips to get to the next digit.

dwightmulcahy, 2019-05-10:
was reading that another option is to do 20 flaps instead, 2 sets of the digits+blank.  was hoping that by doing numbers only that this would help reduce some complexity.  Has anyone tried making a number only one?

tree183, 2019-08-02:
I’ve also been thinking about a number-based one.
I have a deck of cards which are beautiful and using them in a flip clock would be a great way to show them off.
Alternatively to create a single display for all 56 cards (jokers and two extras) and have it rotate randomly would be cool. Any thoughts would be appreciated!
The height and depth of the unit would need to be increased and I think the cards would need to sit in a carriage because I wouldn’t want to cut them or stick them, and changing the deck would be a cool feature!

whitebird, 2019-11-14:
I'm currently working on a fork where i'm tinkering with the variables of the openscad render file to enable a numbers only display.

A few things need to be adjusted to build a display with fewer flaps.
- `num_flaps`- The amount of flaps. I've set this to 11 so i have all digits and a blank one.
- `flap_gap` - The distance between flaps. This needs to increase to avoid the issue where the spool is too small and the flap holes overlap with the strut:
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
- `spool_strut_tab_width` and `spool_strut_tab_outset` - The size of the inner strut and its tab. Needs to be smaller.
- `magnet_hole_offset` - Ensure that the magnet doesn't overlap with the motor, strut and flap holes.
- [Line 978](https://github.com/scottbez1/splitflap/blob/6a04fa0cf2ef832a47301894900d9eb7ea5edac1/3d/splitflap.scad#L978) rotates the motor. This needs to change so the mounting holes of the motor are within bounds. You also need to check if it overlaps with the hall effect PCB.
- Module `motor_mount()` on [line 432](https://github.com/scottbez1/splitflap/blob/6a04fa0cf2ef832a47301894900d9eb7ea5edac1/3d/splitflap.scad#L432) needs to be rewritten to compensate for the new motor position.

It's also a possibility to move the magnet and hall effect sensor to the other side.

This is the intermediate result that I have, but I have to rewrite `motor_mount()` still.
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

My fork is over at https://github.com/whitebird/splitflap
@scottbez1, do you think this would work?

thegamebegins25, 2025-01-07:
@scottbez1 Any updates on this with the upcoming release of v2? I'm also attempting to create a numbers-only display.

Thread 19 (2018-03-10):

double lines in SVG

Neon22, 2018-03-10:
Its possible to save costs in Ponoko and other laser cutters by removing unneeded lines.
If two lines overlap then one can be removed.

I use the inkscape svg templates from Ponoko which scale well (rather than Illustrator tags).
In any case there are a number of lines that are redundant and only one needs to be cut.
Not sure best way to detect and remove from SVG or on export from openSCAD.
I suspect a separate process to remove manually identified lines might be simplest.

scottbez1, 2018-03-10:
Yeah, great point! This note is buried in the README:

Once the combined.svg file is generated, you'll want to manually remove a couple redundant cut lines that are shared by multiple adjacent pieces, to save time/cost when cutting. In Inkscape, select the "Edit paths by nodes" tool and select an edge to delete - the endpoints should turn blue. Then click "Delete segment between two non-endpoint nodes", and repeat this for all other redundant cut lines.

But it would certainly be nicer to do this automatically as part of the export. Not sure the best way, but as you say, it might be easiest to just post-process them somehow.

scottbez1, 2018-05-03:
I've just pushed a commit on a development branch that automatically removes overlapping lines. It's fairly basic, so it only handles overlapping lines where one line fully encompasses the other, but that should cover the common cases. I've also updated the rendering code to highlight the removed lines in red in the raster preview, which looks like this:
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

qwertyaardvark, 2018-05-09:
Aside from Ponoko not willing to even run a drawing with overlapping lines, maximizing the amount of shared lines goes a long way to saving on laser cutting time costs. The attached two layouts of the new gear housing demonstrates this. It started as a challenge to fit all the pieces without taking material out of the main housing panels.

P3 Laser Cost, both fit 8 sets of the housing:
Taking the SVG as shown above and copied 7 more times, butting copies up against each other: $95.57
Placing and fitting all pieces to touch each other as much as possible: $65.87, savings of 31%

[Gearless Housing - Tale of Two Layouts.zip](https://github.com/scottbez1/splitflap/files/1989681/Gearless.Housing.-.Tale.of.Two.Layouts.zip)

Neon22, 2018-05-10:
significant. well done

scottbez1, 2018-09-04:
Going through older issues; just wanted to mention here that basic support for panelizing the design was added back in 4a5fcf6 which allows you to export the rendered 2d design with multiple copies aligned to optimize some laser cut lines. You can do this by passing `--panelize 4` for example when running `generate_2d.py`. Once the panelized design is exported the post-processing step I mentioned above is run, which will eliminate many cases of overlapping straight lines to reduce laser cutting cost. Because of the automated nature of this, it isn't necessarily 100% optimal, but it should handle a good chunk of basic optimization without requiring manual effort.

I'm going to close this issue for now, but feel free to reopen if there are still some specific laser-cutting optimizations that you believe can/should be automatically applied, which weren't covered by the redundant line removal in 2fc1456 or panelization in 4a5fcf6.

Closed 2018-09-04.

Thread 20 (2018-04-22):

Clarification - Motor and Serial

mavbrace, 2018-04-22:
This is a question about sending a message over serial to the units, hoping to get some clarification. Mostly code-related.

We have assembled everything we need to control one node/character from the Arduino. Upon powering up the unit, the purple lights flash and return to orange, giving us the message: 'gave up looking for home’. I've tested our sensor on a separate device and know that it functions. We can also get our single motor to rotate when we enter a '@' into serial. I assume the problem is that the sensor is not assembled behind the gear yet.

The question is, is that assumption correct? Also, do we need a minimum amount of nodes/motors attached for it to function properly?
Also, more importantly, how is the serial communication intended to be used? (i.e. what order did you intend the characters to be sent, eg. the '=').

Really appreciate your work in making a Split Flap Display!

scottbez1, 2018-05-03:
The easiest way to debug a new module is to start with `HOME_CALIBRATION_ENABLED` set to `false` in splitflap_module.h (https://github.com/scottbez1/splitflap/blob/20d789cf1c1a1e8ac40509949c4275f6cd6ed7e2/arduino/splitflap/splitflap_module.h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) - this will cause the module to operate in open-loop mode and ignore all sensor input. So if you command the module to move from A->B the stepper motor will still turn the appropriate number of degrees, but the module won't auto-calibrate to the home position or be able to detect if it's out of sync.

Another thing to note: make sure you set `NUM_MODULES` to the appropriate number (https://github.com/scottbez1/splitflap/blob/20d789cf1c1a1e8ac40509949c4275f6cd6ed7e2/arduino/splitflap/splitflap.ino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). This is particularly important when `HOME_CALIBRATION_ENABLED` is set to `true` - if it's higher than the number of modules you actually have connected, the Arduino will attempt to read additional bytes from the shift register, but its input may be floating, causing erratic behavior as the code thinks that some "ghost" modules are actually hitting the home position unexpectedly at random times.

To test the sensor, you may want to attach a voltmeter or oscilloscope to the sensor pin while everything is connected and then manually rotate the spool so the hole in the gear passes the sensor - make sure you see a good voltage swing on the sensor pin. If it doesn't swing much you may need to increase the contrast between the side of the gear and the hole - try making the hole darker by coloring the walls with black marker if necessary and the side of the gear lighter using paint, white-out, or a white sticker.

The serial protocol is still kind of a mess at the moment, but currently you would send `=` followed by a letter for each module, followed by a newline. For example, `=abc\n` would command the first 3 modules to `a`, `b`, and `c`, respectively. Any additional modules beyond those specific will remain unchanged, i.e. if you were to follow that command with `=x\n`, the first module would flip to `x` and the other two modules would remain on `b` and `c`.

`@` will re-calibrate all modules to the home position, so can be useful when first testing the sensors - you can use this to make sure the home position is reliably detected.

scottbez1, 2018-05-05:
Closing this - let me know if you have any other questions!

Closed 2018-05-05.

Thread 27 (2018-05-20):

Gearless2 - Module-to-Module Connection

qwertyaardvark, 2018-05-20:
I was looking at the design for gearless2, and I noticed the holes that are directly above and below the axle holes for the v0.3 design are no longer there. I presume the holes were for connecting modules together, but the gearless2 design lacks these holes? I can see that the lower holes had to go b/c the PCB was moved down there, but the upper holes likely could stay. Maybe the lower holes could be between the backstop bolt slot and the bottom plate holes?

Not sure if you had another idea in mind for connecting the modules, but I have added these holes back in my svg files.

scottbez1, 2018-05-22:
You're right - the connector holes were removed in 0ec4b1e - the issue is that with the updated design there's no longer room for a bolt head between flaps and the wall opposite the motor, so you couldn't actually put a connecting bolt there any more:
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

The other, smaller issue is that the walls were moved closer towards the flaps, so the distance between adjacent walls has increased to over 16mm, so either connecting bolts would require a separate line item on the BOM for a longer bolt, or else the "standard" M4 bolt would need to be changed to something quite a bit longer.

So for now I've omitted them while thinking through some alternatives, as I don't think it's a show-stopper to lose the connections for now (in an actual installation with multiple units there probably needs to be a way to attach the modules to the structure as well, not just to each other, so I'd want to tackle both of those issues at the same time)

One idea would be to laser-cut a "bridge" that could press-fit onto the top and bottom via some slots cut into the side walls, something like this:
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

Or it might make sense to somehow extend the top and bottom enclosure pieces horizontally so they meet the adjacent unit and then somehow allow those to be connected together. In any case, I haven't given this a ton of thought yet, so I'm open to other ideas.

qwertyaardvark, 2018-05-22:
On a smaller scale and based on the assumption people will make multiple modules, I am planning on making the front bezel a single piece for multiple modules. I can fit up to 9 module bezels in a row in a Ponoko P3 sheet, but will likely reduce it to 8, as that's how many modules I can fit on a P3 sheet anyways. Alternately, I may make 2 4-character bezels to match the capacity of a controller. I would leave the nodes for individual modules so that smaller or individual bezels can be made.

Past 8 modules, there still needs to be way to connect between modules. I personally think there is still enough space between the flap exclusion zone and the top enclosure piece for a longer connecting bolt. It would require a new part on the BOM, so I will think about other mounting methods. For me, it wouldn't be a big deal to source a longer bolt, and that is what I'll go with for now. I do like your bridge idea, as its much easier to apply and remove.

For one of my applications, I intend on not having a structure to save material costs and will mount directly to the modules at their bases (1 row x 12 modules). For the application of a large board (4+ rows x 20/24 modules) that will hang off a wall and needs a structure, I am torn between these two choices:
* integrate the overall structure into each module
  * higher material cost per module
  * more difficult to replace a single module
  * simpler to design/assemble module-to-module connection
  * highly modular number rows/columns
* making a separate structure that will hold the modules
  * has to be custom designed for a size
  * complexity of structure and module-to-structure interface design
  * overall lower material cost and weight
  * easier to replace a module

I would like to go the route of making the structure integrated into each module. Will keep the concept in my head and let you know what I come up with.

scottbez1, 2018-06-04:
My plan right now is to add two related connection components to the design, which are designed to allow the modules to mount to an external structure with proper alignment and spacing. It will _not_ enable modules to be directly connected to one another to form a rigid structure on their own.

The reason for this is that an external structure can be as simple/cheap as a rectangular plywood base board for them to be screwed down into. It also means it will be much easier to access/service individual modules.

My planned changes are:
- add a simplified version of the "bridge" connector I mentioned above. I plan to have one at the top and one at the bottom. This will press fit (or may even be loose and simply sit in place depending on tolerances of laser cutting, but that's fine) and is only intended to maintain spacing and alignment in the XY plane
- add a single 4mm/M4 hole, centered in the X dimension, in the top and bottom walls, which will allow the modules to be mounted to a board above or below if desired. Having just a single hole would allow rotation about the Z axis on its own, but the bridge connectors should prevent that rotation

On a larger display, I'd imagine the best way to mount modules is probably to have a single front panel for a group of modules (e.g. something like 2 rows x 8 columns per front panel, depending on how many can fit in a single laser-cut), and each module mounts to that front face simply using the existing 2 front screws + tabs and nothing else. That would also allow individual modules to be serviced or replaced by removing the 2 screws and pulling it out from the back. The removed module won't have the rigidity provided by the front face, so could potentially parallelogram a bit, but that's probably not a huge deal; you could always slip on an individual front face to hold everything square while testing/repairing the innards of a single module.

scottbez1, 2018-06-04:
I've pushed the initial changes to the 3d design in ad89cf78a07d8c13f3687d7be0f420d4e2130e40

The connector bracket fits in place like so:
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

It's held in place by 2 locking tabs that stick inward and latch into a small hole on the inside of the wall. Here's what the bracket looks like when it's not in place - you can see the locking tabs a bit better:
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

scottbez1, 2018-06-06:
I landed the 2d update in b20415945d8a6b9d5907e3c98b3b7a8898dec790 and am awaiting a new order from Ponoko. Closing this for now but will reopen if any issues come up when I get the new design in a few days.

Closed 2018-06-06.

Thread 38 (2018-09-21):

Documentation on ordering parts needs improvement

scottbez1, 2018-09-21:
As @mflmartin helpfully highlighted to me, the documentation around ordering the electronics components is somewhat outdated, and has a number of assumptions baked in that may not be obvious.

I see two main issues:
- The relationship between the number of modules, the number of controller boards, the number of sensor boards, and the amount of supporting hardware needed (Arduinos, power supply amperage, etc) is unclear. This needs its own wiki page, ideally with supporting diagrams of different example cases (HELP WANTED for good looking vector graphics for this!)
- the electronics BOM is auto-generated, but doesn't clearly explain what components it includes and whether all of them are actually necessary. I.e. it currently includes all components that might be needed for either an A, B, or C variant controller board (when in reality you only need some subset, depending on which variant you're making) and enough parts for 4 sensor boards (which you may not need if you're making fewer than 4 modules). It may make sense to simplify things to 2 variants: a "shield" ("A") and "expansion" (currently "B") variant. It may also make sense to either auto-generate an Excel spreadsheet with formulas for calculating part quantities based on # of modules, # of "shield" variant boards, and # of "expansion" variant boards, or else maybe create a BOM wizard on the project website to do those calculations based on the generated .csv?

martinlombana, 2019-01-20:
I also wanted to know if we must modify something for 3mm sheets, as I want to do them in acrylic.

Thanks!

scottbez1, 2019-01-22:
Oh, interesting! Let me know how it turns out! I may try ordering some 3mm acrylic as well just to see how that works

scottbez1, 2019-01-31:
@whitebird - are you still seeing that permission error? I just tested the link in an incognito window and it seemed to work fine.

If you're still hitting the 403 error - are you logged into a Dropbox account? Can you try opening it in an incognito window if so?

whitebird, 2019-02-01:
@scottbez1 It's indeed only an issue when I'm logged in. Thank you!

ArwedSchmidt, 2019-02-15:
@scottbez1 The MDF parts arrived (some delay due to customs over here in Germany) and I gave it a first try - looks like 3.0mm is just fine. Everything was a kinda tight fit so I had to use some gentle force but I guess that's how it's supposed to be

ericyeargan, 2019-07-16:
Hmm, 3.2mm MDF no longer seems to be available in the US either: https://make.ponoko.com/materials/mdf-fiberboard

Oddly enough the ["show-material" URL](https://www.ponoko.com/make-and-sell/show-material/64-mdf-natural) that @scottbez1 posted _does_ show 3.2mm but I suspect that page is no longer valid - it redirects to the main page if you're logged in.

@ArwedSchmidt, when you ordered 3.0mm MDF, did you modify the SCAD to use 3.0mm thickness and regenerate the SVG or just submit the 3.2mm release version?

scottbez1, 2020-04-18:
Closing this issue for now. Keeping #76 open to track the 3.0mm MDF documentation update.

Closed 2020-04-18.

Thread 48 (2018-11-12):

v0.5 Laser parts offset

henricazottes, 2018-11-12:
Hi,

I cut a set today and after assembling parts, I see a small offset of the wheel regarding the front hole:

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

The blue space seems fine but the red one seems a bit too much. Flipping the front panel was even worth. Is the assembly incorrect or is there an error in the file ?

Thanks

scottbez1, 2018-11-12:
It looks like you have the spool outer disk and the inner square piece
(that the bolt attaches to) swapped - the smaller square piece should be on
the inside of the spool disk.

See https://youtu.be/zHM8W6Rm2i4?t=136 for assembly instructions (sorry I
haven't yet linked to this video from the project wiki).

On Mon, Nov 12, 2018, 10:03 AM Henri Cazottes <notifications@github.com
wrote:

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

henricazottes, 2018-11-13:
Thanks, I could have guessed it...

Another question: the video made me realize that magnets are missing from parts list. What ref should I look for ? The hole is 3.7mm wide but it didn't give me a lot results.

scottbez1, 2018-11-14:
It's a little odd, but the magnets are actually in the electronics BOM since I originally used this magnet from Digikey -- [469-1027-ND](https://www.digikey.com/product-detail/en/radial-magnet-inc/9027/469-1027-ND/5218822) a 4mm diameter x 2.5mm neodymium magnet.

I've also had success with some cheap 4mm x 1mm round neodymium magnets from AliExpress as an alternative. You could probably also get away with a small cube magnet (gluing it in place if needed) or drilling the hole bigger and using a bigger magnet. As long as it's strong enough for the hall-effect sensor it shouldn't matter too much. And the hall-effect sensor can be moved within its mounting slot, so there's nothing particularly precise about where the magnet is mounted on the spool; the sensor can be shifted forward or back as needed to fine-tune.

scottbez1, 2018-11-21:
Closing this issue to tidy up the issue tracker since I think I answered your questions, but please feel free to open a new issue if you have any more questions, more than happy to help :)

Closed 2018-11-21.

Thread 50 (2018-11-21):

Add a motor direction constant to reverse motor rotation if needed

henricazottes, 2018-11-21:
Hi,
I assembled a board and tested it with one digit. Everything looks fine except the motor rotation which is reversed. A quick look in the code didn't reveal any setting for that. Any clue?

I have the 5v version by the way.

vettorazi, 2018-11-21:
hey! did you checked the pins from the board to the arduino? the motor are in the right side (forward to you?)

scottbez1, 2018-11-21:
I've gotten one batch of motors that turned the opposite direction for whatever reason. These things are so cheap and I think manufactured by a bunch of different companies that you tend to get slightly different products from different vendors. That said, you can change the direction in code fairly easily by reversing the elements of the `step_pattern` array in splitflap_module.h:

https://github.com/scottbez1/splitflap/blob/ec1b76c90de9fa56e2e0075ef8a7e6e88a0664d0/arduino/splitflap/splitflap_module.h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

Another thing to keep in mind is that there are two different gear ratios I've seen in motors, as mentioned on the [Motor Info](https://github.com/scottbez1/splitflap/wiki/Motor-info) wiki page, so you may need to change the `_GEAR_RATIO_INPUT` and `_GEAR_RATIO_OUTPUT` values as described in the comment here: https://github.com/scottbez1/splitflap/blob/ec1b76c90de9fa56e2e0075ef8a7e6e88a0664d0/arduino/splitflap/splitflap_module.h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

The non-integer 63.684:1 gear ratio seems to be much more common in the 5V version of motors, so you may want to check for that as well if the motor doesn't seem to be aligned right after several full revolutions.

And one question out of curiosity - is the order of wires on your motor connectors Red, Orange, Yellow, Pink, Blue?

henricazottes, 2018-11-23:
Thanks, reversing the `step_pattern` did the job.
``` c++
const uint8_t step_pattern[] = {
  MOT_PHASE_D | MOT_PHASE_A,
  MOT_PHASE_C | MOT_PHASE_D,
  MOT_PHASE_B | MOT_PHASE_C,
  MOT_PHASE_A | MOT_PHASE_B,
};
```
Didn't have to touch gear ratio. And yes, colors are in the order you mentioned :)

scottbez1, 2018-12-03:
:+1:  Going to change the title of this issue to make it a feature request for adding a direction toggle to the code. It really should be easier to flip the direction than reversing an array.

Closed 2019-01-05.

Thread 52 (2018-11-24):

home sensor

carlosbritotx, 2018-11-24:
Hi friend, could you explain the code for your home sensor? I'm using a nema 17 engine instead of yours. I want help to understand the code of your home sensor. Could you explain me. Congratulations on the project.

scottbez1, 2018-12-03:
Here's a really rough summary of what all the SplitflapModule does to drive a splitflap motor and account for home sensor feedback:

It drives the motor based on a commanded flap index, which requires keeping track of the current step/phase as well as the motor position, and calls to update() check to see if it's time to advance to the next step (based on the distance to the desired flap and an acceleration curve from acceleration.h).

This gets somewhat complicated because the 28BYJ-48 motors sometimes have non-integer gear ratios resulting in a non-integral number of steps per spool revolution. Because of this, the motor position is tracked in terms of steps (`current_step`), which can be converted to a spool position by dividing by the gear ratio. Making matters worse, however, is the fact that floating point math is expensive on the Arduino, so the code has been optimized to use integer math instead (which generally means keeping a numerator and denominator as separate integers rather than calculating a floating point quotient). This is why there's quite a bit of additional confusing math throughout.

The way the home sensor interacts is that once per revolution the code calculates the step index where it expects the home sensor to be triggered (`expected_home`) and from that it calculates 3 important indices: `unexpected_home_start_step`, `unexpected_home_end_step`, and `missed_home_step`. The "unexpected_home" values are a range of step indices where it would be "unexpected" for the home sensor to be triggered (i.e. something weird happened and the spool got to the home position EARLIER than expected). The `missed_home_step` is calculated to be  slightly after the `expected_home` position; if the controller gets to that step without the home sensor being triggered then something went wrong and the spool didn't rotate far enough. For reasons that are slightly complicated (related to the gear ratio stuff mentioned above), all of the step indices are computed _modulo_ 2 * GEAR_RATIO_INPUT_STEPS, which you may see scattered throughout the code.

In any case, I think to support a NEMA 17 motor (assuming your motor controller has STEP/DIR inputs) you could probably modify `STEPS_PER_MOTOR_REVOLUTION` to be the motor's rated steps per revolution (which is probably something like 200) and then set `_GEAR_RATIO_INPUT` and `_GEAR_RATIO_OUTPUT` both to 1. Then you'd want to remove the SetMotor method and replace where you see `current_step++` with a pulse of the STEP pin to the motor driver. In theory all of the sensor code should still just work, but I've never tried a different motor like this.

carlosbritotx, 2018-12-03:
Thanks for the comment, I'm taking the first steps on the arduino. I'm using the a4988 and nema 17 4-wire drive, I'm kind of confused in the code, esou using two 20-tooth pulleys and a strap, my reel has 30 tabs, could you help me with an example code, is not able to use your code here on my. Many thanks friend.

Closed 2020-04-18.

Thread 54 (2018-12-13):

Particle support

scottbez1, 2018-12-13:
Was discussing support for Particle boards with someone over email; moving to the issue tracker to make that discussion public and keep a running log of progress/pitfalls of getting a splitflap running on Particle in place of an Uno.

>Assuming they can be programmed with the Arduino IDE and they have hardware spi that's at least as fast as an Uno I think it should be doable.
>
>The control board connects to the Arduino Uno by plugging into the ISP connector (for hardware spi access) and 3 digital pins (there's nothing particularly special about the choice of those pins IIRC). It also plugs into the VIN and GND pins, but you won't need to connect those (there's a ground connection on the ISP header, so no real need for another one, but it made sense to use a 2pin header rather than a single pin header for VIN by itself) - that just allows the motor power supply to optionally be fed to the Arduino's VIN if JP1 is installed, which makes it easy to run the Arduino without a computer connected via USB.

>I just remembered that you'll probably need to edit spi_io_config.h since it currently interacts with the sensor and motor latch pins using pinMode as well as direct port manipulation. You might be able to get away with a digitalWriteFast or something to replace the direct port manipulation (OUT_LATCH_PORT and IN_LATCH_PORT), since I'm not sure if there's an easy drop-in replacement on particle boards.
>
>Also, if you try running it on a particle and the motors end up missing steps, it might be worth trying a lower top speed by editing generate_acceleration.py to increase MIN_PERIOD_MICROS, and then run it to regenerate the acceleration curve (make sure the Arduino IDE is closed because it doesn't like files changing in the background).

scottbez1, 2020-04-18:
Closing for now. No plans to add support for Particle boards at the moment.

Closed 2020-04-18.

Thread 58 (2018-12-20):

Kicad 5

scottbez1, 2018-12-20:
The electronics projects are currently Kicad 4, but Kicad 5 is the latest version.

It would be nice to update all of the files to Kicad 5 and then verify that the schematics, footprints, and pcbs, along with all the Travis CI integration, still work correctly.

whitebird, 2019-02-04:
I've opened up the sensor PCB in KiCad 5. When opening a 3D view it throws the following error;
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

This is probably due to the yellow lines from the Edge.cuts layer not being a closed square. Can this be for mass producing the piece? I don't have KiCad 4 to compare the issue.

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

scottbez1, 2019-02-04:
Yeah, those weird edge lines were from early experimentation with panelizing the board. IIRC the current panelization script ignores the original board outline layer entirely and redraws new lines based on the panelization parameters, but I'm not at my computer to double check at the moment. Regardless of the current behavior of the panelization script, the right thing to do is to fix that board outline, so I'll make a note to take care of that at some point.

scottbez1, 2021-05-08:
Closing in favor of #138

Closed 2021-05-08.

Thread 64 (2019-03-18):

ESP32 support

DrSkunk, 2019-03-18:
As referenced in https://github.com/scottbez1/splitflap/issues/55 , the ESP32 is the successor for the ESP8266.

One of the issues is that there isn't a board like the Wemos D1 mini that is as ubiquitous.
An alternative is to create a board to solder the ESP32 directly, but that would require a 3.3V regulator as well as a programmer chip and a USB port.

whitebird, 2019-03-19:
To me it seems this version of the board seems mostly used: https://www.aliexpress.com/item/ESP-32S-ESP-32-Development-Board-WiFi-Wireless-Bluetooth-Antenna-Module-For-Arduino-2-4GHz-Dual/32898649271.html

scottbez1, 2020-04-28:
Starting to think through this a bit more as part of a plan to support larger displays - https://paper.dropbox.com/doc/Splitflap-large-scale-driver-project--Ay7kxGjRClsCtJ6qnOOqLQeOAQ-rUpovQ77LuERHKwqJLcEH

I'd separately like to consider an ESP32-based driver board that's still hobbyist-friendly (i.e. through-hole components), just because of the benefits of having wifi or bluetooth available for control out of the box, but for now I'm focusing on supporting larger displays.

SamWarmuth, 2020-04-28:
The combination of an ATTiny88 ($1.50, through-hole) and a TPIC6b595 (also $1.50, through-hole) for daughter boards that can each control two displays and a ESP32 running the show over I2C seems like a strategy that would work. Having a single ESP32 that drove all of the displays directly means *lots* of long wires that are pulling real amounts of current. If each of the control boards is all near its motors, you just need a single signal wire bus.

There's some more info/pictures in my previous post: https://github.com/scottbez1/splitflap/issues/66#issuecomment-549174768

I haven't had time to get any farther on the project, but I just made my repo public in case it could be useful to anyone: https://github.com/SamWarmuth/SWSplitFlap

scottbez1, 2020-04-28:
Nice, thanks for sharing - I'll have to poke around your repo next weekend. I've linked your comment and repo on the planning doc.

I don't have experience with I2C over longer distances, so I'd be somewhat worried about potential issues sharing a long I2C bus across a big display, but not sure how much of a problem that would actually be. Did you do any tests with longer cables to see what distance you can get?

My other concern would be programming that many devices in the large display - with a 120 character display I'm looking at building, that's 60 MCUs, so would probably want to have a custom bootloader so all MCUs can be programmed via the bus (and ideally can be programmed in bulk rather than one-by-one).

SamWarmuth, 2020-04-28:
I didn't test with long distances, but I had no trouble at around 6-12". The internet says up to [a few of meters](https://electronics.stackexchange.com/questions/106265/maximum-i2c-bus-length) is pretty straightforward.

Split flaps are a pretty good use-case: each PCB along the way repeats the signal, so the distances are individual, not cumulative. Also, we're transmitting really small amounts of info (e.g. "move motor 7 forward 300 pulses" is only a handful of bits depending on how you encode it), so we can use a lower bitrate with more error correction.

Programming is definitely a sticking point. With through-hole components it shouldn't be too hard to use a [ZIF socket](https://en.wikipedia.org/wiki/Zero_insertion_force) connected to a programmer to write them all. There are boot loaders you can use to [write firmware over i2c](https://hackaday.com/2018/10/20/i2c-bootloader-for-attiny85-lets-other-micros-push-firmware-updates/), but if you have to write that firmware on their in the first place, the main thing that gives you is over-the-wire updates.

scottbez1, 2021-03-25:
Closing this, as initial support for ESP32 has been implemented in firmware for a while now.

Regarding the other discussion around large displays and ESP32 support, the new [Chainlink Driver board](https://github.com/scottbez1/splitflap#chainlink-electronics) is being designed for this purpose (using shift registers and an SMD design that's relatively cheap to order mostly-assembled), along with a Chainlink Base board which will eventually host the ESP32.

Feel free to open new issues if there is any specific ESP32 functionality still missing or desired.

Closed 2021-03-25.

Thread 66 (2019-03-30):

Large Display (>12 characters)

barkerb1, 2019-03-30:
Any thoughts on scaling beyond a single Arduino?  Would a Mega or Duo board allow for more controllers per micro-controller?

My initial thought would be to use a RasberryPi to daisy chain each Uno's 12 characters and also serve as a small web server for remotely controlling a large display.  I'm going to start with connecting 4 controllers (16-char) and two Uno's so I can start working on the Pi.  If successful, I plan to integrate it with my Google home and scale up to something big enough (100+ char) to display Tweets, song titles, news headlines, and stock tickers on command.

SamWarmuth, 2019-03-31:
I'm working on a build using an ESP32 and MCP23017 i2c port expanders (16 new pins per chip). You can use up to eight expanders to get 128 GPIOs. The ESP32 is a *lot* faster than an Uno, so you should be able to drive more concurrently —  not sure how many it would max out at though.

Semi-unrelated, but if you're going to be running that many characters, you might want to take a look at the TPL7407L for driving the steppers — it uses NMOS transistors instead of darlington transistors, it should run cooler (and use less power).

scottbez1, 2019-03-31:
The 2 main limits of the Uno are memory and clock cycles. A Mega won't help with the clock speed constraint so I don't think you'd be able to add many additional modules, if any. Both the Due and ESP32 are likely good options for controlling more modules, though connecting multiple Uno's to a Pi should also work fine if you've already got those handy. For a big display with 100+ characters you'd probably want to drastically rethink the electronics to make it easier to build/control and cheaper (this design is really optimized for small hobbyist production).

barkerb1, 2019-04-01:
@scottbez1, I'm not thinking of building something commercially viable, simply a one off display to hang on my wall with the added cool factor when I have guests over of being able to talk to it.  Using a Due is intriguing, if it could run at least 6 controllers (24 characters, one row) per board then I would only need 4-5 to run the whole display and would only need marginal tweeks to what you've already created.

@SamWarmuth, I'd be interested in possibly using the ESP32 if you're willing to share your fork of the project.  Honestly, I'm trying to put as little time investment into the electronics as possible so I can invest my time into the software and connecting it to the cloud, which I'm also willing to share if anyone wants it.

I just finished soldering the boards for 16 characters to begin experimenting, happy to collaborate if anyone's interested.

peazley, 2019-11-03:
@barkerb1 @SamWarmuth have either of you made progress for supporting a larger set of characters?  I'm really curious about using an ESP32 for this.

SamWarmuth, 2019-11-03:
Unfortunately I haven't had a lot of time recently to work on this in the last few months.

I ended up designing my own PCB that uses an ATTiny88 and a TPIC6b595 to drive two boards, controlled using an ESP32 over I<sup>2</sup>C. Since the ESP32 is just sending high-level commands to the ATTiny (e.g. "Move to position 13"), the CPU load is really minimal. The only issue you'd run into is the max number of I<sup>2</sup>C slaves, which is 127. But that just means you need one ESP32 for every 127 characters you want to display (or maybe come up with a more complicated I<sup>2</sup>C hierarchy).

I also ended up redesigning the enclosure to be fully 3D-printed, to save on assembly time/effort/price (I own a printer). My estimate using this system was that I could get the price-per-display down to $6 or $7. I haven't had time to clean everything up and build more than a couple of the displays. I'll have more time to work on projects like this as it gets colder out and I spend more time inside.

Unfortunately it's not in a great place to share right now, but if there was some interest I could try to get something published.

Here are a few pictures showing the different parts:

Driver PCB
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

Fully 3d printed spool/frame:
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

With numbers:
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

benlongo, 2020-02-10:
Hey Sam, thank you so much for publishing this awesome project! I’d love to see the new designs you have been working on, even if they are in quite rough form.

SamWarmuth, 2020-02-11:
Splitflap is all `scottbez1`'s work, I'm working on a new build that takes a lot of inspiration from his. I'll see if I can get the files in a better state and publish them soon.

scottbez1, 2020-04-18:
Cleaning up old issues. I think the main questions have been answered here. Please comment or open a new issue if you still have outstanding questions, thanks!

Closed 2020-04-18.

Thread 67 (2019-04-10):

Bigger Displays (150x100mm cards)

gollou, 2019-04-10:
I'm trying to scale up each module so they can be readable from further away, I think I'll get each A6 card by cutting some A4 sheets into 4 ([aliexpress link](https://www.aliexpress.com/item/ID-card-making-supplies-material-Blank-Inkjet-print-PVC-sheets-A4-50sets-white-color-0-76mm/32825311077.html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))
Each module should then be A5 size : 148x210mm

But I’m wondering if any of you has experimented the design with that big letters and if you can foresee any issue coming : will it be too heavy for the motor, will the wheel be big enough to resist the weight, will the 1.4mm plastic holder be resistant enough for the weight, should the depth of the box be increased ?

SamWarmuth, 2019-04-10:
I haven't tried letters that big before, but I suspect your biggest issue is going to be motor torque. The standard card flaps are about 23 cm² (4.28cm x 5.4cm), yours will be 156 cm² (10.5 x 14.9). That means each flap will be almost **seven times** heavier.

Stepper motors have more torque when they move more slowly, but I'm not sure it would ever have enough strength to move those flaps. There are more powerful motors available, but they'll cost more and will require a bit of redesigning.

scottbez1, 2020-04-18:
Cleaning up old issues. Thanks @SamWarmuth for answering this one! Motor torque is definitely a concern with larger letters - the cheap 28BYJ-48 motors are already pretty much at their limit with the current credit-card sized flaps, so you'd probably need to switch to a proper stepper motor and stepper driver to go bigger.

Closed 2020-04-18.

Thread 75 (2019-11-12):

Possible easier calibration?

cstarkers, 2019-11-12:
I’m just wondering if anyone has attempted to implement a simple switch as a calibration device? I’m thinking a piece of wire glued along the top front edge of a flap, and contacts on the inside of the top of the front face.  When the previous flap falls, the wired will bridge the contacts. Seems simpler and cheaper than IR/Hall effect, as it would only require a few bits of wire and 1 component (pull up or pull down resistor).

I haven’t built my display yet, but I’m planning to soon.  Unless someone can point out something I’m overlooking, I intend to attempt this and report back.

My apologies for not attempting to draw it up, but my CAD is not up to that.

scottbez1, 2020-04-18:
Sorry for responding so late. It's an interesting idea, and I'd love to hear how it turned out if you ended up trying it.

I'd be worried about getting calibration accurate enough that way though -- with 40 flaps there's bound to be some slight variation in when they flip down, so you generally want to make sure the motor is aligned with the middle of the "acceptable" region when calibrating. Otherwise, many of the flaps will flip correctly, but some flaps that are aligned differently or slightly larger or smaller either won't flap when they're supposed to (if the motor stops early) or will flip down before they're supposed to (if the motor moves too far for a given flap). The hall-effect sensor allows you to really finely adjust the calibration position to make sure it works for all 40 flaps.

Closing this issue for now, but I'd love to hear if you tried it and how it worked!

SyntaxColoring, 2020-05-06:
There's an expired 1973 patent, [US3771242A](https://patents.google.com/patent/US3771242A/en), that used notches cut on the top of each flap to selectively engage an array of sensitive switches. The motor would turn until the switches matched the code it was expecting.

With software, you could probably get away with 2 switches. The first switch would be engaged only by one flap, for homing. The second switch would be engaged by every flap, to let the controller adapt to minor variations in how different flaps flip.

cstarkers, 2020-05-06:
That patent is a very interesting idea, thanks for bringing it to my attention.

I have had to put my version of this on hold for a while, but I fully intend to get back at it once Covid abates and I have laser cutter/3d printer access again - I will get back to you if I have any success.

Closed 2020-04-18.

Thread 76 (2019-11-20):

Using 3.0mm MDF (Ponoko no longer carries 3.2mm)

ericyeargan, 2019-11-20:
The OpenSCAD script and ordering guide specify 3.2mm MDF for the laster-cut parts. Unfortunately, it looks like Ponoko no longer carries 3.2mm. In some commentary in the ordering guide @scottbez1 suggests that it's possible that the material was always 3.0mm and that the Ponoko was just listing it incorrectly as 3.2mm.

So, I tried ordering a parts using 3.0mm MDF with the latest release but things don't fit quite right - there are visible gaps in the slots and a good amount of give when you lightly twist the spindle. (FYI, when measuring the material thickness with calipers, it's right around 2.99mm).

I've also tried modifying the OpenSCAD to change the material width to 3.0mm and update the kerf. I ordered parts with that updated pattern and things fit better although there's very little/no clearance between the spindle and sides. I had to reduce the top spindle speed to keep the motor from stalling - I suspect because the spindle is rubbing slightly against the sides. You can view the commit with the OpenSCAD change [here](https://github.com/ericyeargan/splitflap/commit/0d5985a39a45576651774b16db48451103f24ab1).

Curious if anyone else has dealt with this. My ultimate goal is to build 12 modules. Right now, I'm trying to decide wether to mess with the 3.0mm SCAD to increase the spindle clearance or to just live with a loose fit on the 3.2mm SCAD (maybe through some liberal CA glue application).

P.S. Despite these issues, I've been having a blast with this project. Thanks @scottbez1 and all of the contributors!

whitebird, 2019-11-21:
Ah, weird, I cut out from 3mm myself and it fit very well together. Maybe there is a kerf difference between my lasercutter, a trotec speedy 300, and the one ponoko uses.

ericyeargan, 2019-11-21:
Thanks @whitebird. I should note that I haven't actually built the entire module with the unmodified pattern. Maybe I'll find that it works just fine once everything's bolted together.

ericyeargan, 2019-12-18:
The Ponoko 3mm ended up working pretty well. I did have to apply some glue to the spindle joints. Otherwise, it would get out of wack if you applied even a little torsion to the sides. The only other issue is that the tabs stick out very slightly from the front panel/face. That probably wouldn't be an issue for most people but I'm thinking about covering the fronts in a wood veneer so I need it to be fairly flat. It's easy to sand those down though before attaching the front panel.

I'll leave this issue open in case @scottbez1 wants to update the ordering instructions. Otherwise, feel free to close.

Closed 2020-11-27.

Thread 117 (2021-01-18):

SplitFlap Display has three strange behaviors

daniele8808, 2021-01-18:
Hello Scott, It's been a long time and I would like to finish this project started more than a year ago. I have completed the construction of a module and mechanically it should be ok, I have also done some tests with the sensor and it is correctly detected but I still cannot see the letter I want on my display. In this short video I show the three problems I'm having:

https://youtu.be/BHOUhOT_epA

- 1 error: often when I select a letter to view the display freezes after 2 steps for no reason
- 2 error: if I try to display a character that is too far from the starting point (for example I switch from A to Z), the display makes a complete revolution and returns to A, but no errors are reported on the console
- 3 error: a few times when I recalibrate by entering the @ the display arrives at the home point and adds a micro step that changes the initial letter

I would be really grateful if you could help me complete this project.

dmadison, 2021-01-18:
It looks as though the display is binding at 'A'. [Look closely around 38 seconds](https://www.youtube.com/watch?v=BHOUhOT_epA%3Ft%3D&t=37s) - it holds the 'A' position for ~2 seconds before it relaxes, which indicates that it's trying to move the spool but can't. I've noticed a similar phenomenon on my own test modules when the spool gets out of position.

Scott may have better advice, but I'd start by checking that the flaps aren't hitting the enclosure anywhere except at the very top edge.

daniele8808, 2021-01-20:
thanks for the advice, I try to cut the displays again using the v.6 but if the problem was the beat of the cards it would solve only one of the three problems I am having. Let's say that the main problem I'm having concerns point 1. I still can't get the letter I want to display, it works randomly and resets itself continuously.

scottbez1, 2021-01-21:
My guess is that the motor is stalling/skipping due to not having enough torque at the higher speed. The behavior you're seeing is that the module will always rotate slowly (which has more torque) when it is searching for the home position at startup (or if it detects an error while moving it will also search for the home position before continuing), and then once it's found it will return to normal mode and accelerate up to full speed to go to the desired flap. It seems like everything works fine until it starts accelerating, so the first thing I would try is to reduce the speed - the default values are fairly aggressive and may not work if there is more friction, or you have a slightly different motor, etc.

You can reduce the top speed by closing the Arduino IDE, then edit generate_acceleration.py (should be in the same folder as the arduino code) to change the MIN_PERIOD_MICROS value - maybe try setting it to 2400 to start, which should be half the default speed. Then run that script (should be directly executable on Mac or Linux, or you may need to invoke it via python from the command prompt on Windows), which will generate a new acceleration curve in acceleration.h. After that you can re-open the Arduino IDE and upload the code again and test it. If that works you can try some lowering the value again to find the fastest speed your module will allow reliably.

daniele8808, 2021-01-25:
Hi Scott, thanks for your reply and time.
I've done what you told me but I think I have two problem at the moment:

1. mechanical problem
2. connection/software problem

- Regarding the first problem I tried to make the change via code you told me by changing the value in the python file but without success. In the end I decided to cut the new version of the project the V 6.0 where I saw you moved the motor by removing the two gears (so as to eliminate the friction problems I had) and I will also buy the 12 Volt motors (more powerful).
I hope to cut the new part in this week and make a new test.

- Regarding the second problem the few times that the gears turn well and I have no problems with attractiveness, however, I find it difficult to visualize the required character and I don't understand why. As you can see from this second video some times I specify the character that I would like to display but it is not printed in the console, instead I display an empty string. Does it happen to you too or do you know why?

here a video of this second problem: https://www.youtube.com/watch?v=e1L3PMftkNk&feature=youtu.be&ab_channel=DanieleMartini

dmadison, 2021-01-25:
For the second problem, in your video you're typing spaces between `=` and the character you want to send. The firmware is interpreting that as you want to write the space character to the first module (and the character you typed to the second). You have to send the command without any spaces.

daniele8808, 2021-02-02:
Hello Scott, I finally finished my display but I need help for the last time. Here the display -> https://youtu.be/7kNUpaLQhlQ
I read your guide about calibration but I can't display what I want.
All the sensor looks work.
What do you think is the problem?
Thanks in advance for any help

Daniele

daniele8808, 2021-02-05:
Ok I think I foud the solution By myself. The cards I cut are not very accurate so this creates small malfunctions in the system, but all in all it seems to me to be working. This weekend I try to make new cards and improve the functioning of my display. In the meantime, I made this little video to thank Scott for This beautiful project.

https://www.youtube.com/watch?v=u_ax8iPwcRU&feature=youtu.be&ab_channel=DanieleMartini
https://spinzam.com/shot/?idx=254804

I have only one last question, in the latest version 6 code I saw that a piece of code concerns a bluethoot connection with the. ESP32 module. Is there any documentation on how to integrate this module as well?

Thanks in advance for everithing
Daniele

scottbez1, 2021-03-05:
Daniele, I just noticed when watching your latest video - I think the front faces on your modules are installed upside down/inside out.

The taller portion should be on the top, and the shorter portion on the bottom.
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

If you flip the front face vertically (so the side that was facing in now faces out) I think that may help with reliability, as it will hold the flaps back more consistently at the top. See https://youtu.be/UAQJJAQSg_g?t=36 for a demonstration of why that position is key to reliable behavior.

(it's unfortunate that the design is subtly asymmetric like this, but @dmadison has smartly [added engraved orientation markers](https://github.com/scottbez1/splitflap/pull/111) in an upcoming revision of the hardware design so it's hopefully easier to notice in the future)

daniele8808, 2021-03-13:
............. :-) ok thank you Scott. I'll fix it and see if my display start to work better making this change.
Meanwhile I already started to build my second display. I'll pay more attention during the assembling process.
Thanks

Closed 2021-03-13.

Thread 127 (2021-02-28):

3D Printer?

ezorita, 2021-02-28:
Hi Scott, this is a fantastic project. Thanks for your contribution.

Not sure if this has been asked before. Is there an easy way to export the laser cut model to 3d printed parts?

lastcoolnameleft, 2021-03-05:
@ezorita I have been working on exactly this.  It is possible; however, there's some gotchas that I haven't quite solved yet.  My spool doesn't seem to spin as loose as the laser cut ones.  I'm sure I could change some of the dimensions, but it's quite time consuming.  I've modified his splitflap.scad so that I can 3d print the flaps, spool and frame.  Let me know if you're interested and I can share with you my findings so far.

And yes, this is an exciting project and I think some others have tried 3d printing it, but I haven't seen any final product of it yet.  I feel like I'm close, but the tolerances are really low.

ezorita, 2021-03-08:
hey @lastcoolnameleft it's great to hear you already made some progress on this! I did start to adapt the different frame parts to 3d printable objects.

It would be great if we share our progress, I'll try to improve upon the printing tolerances. Would you like to fork the repo so that we got a place to contribute and eventually open a PR back to @scottbez1?

dmadison, 2021-03-08:
For what it's worth the flat laser-cut design should work (nearly) out of the box for 3D printing even though it's not designed for it. Within the `splitflap.scad` file you need to modify:

```
render_3d = false;
kerf_width = 0.5;  // spacing between parts
```
And you'll get the entire 3D design packed flat which you can export as an STL for printing.

The one exception is that one of the spool struts is placed on top of the right side panel so it's cut out of it on the laser. You'd have to reposition the strut somewhere else.

scottbez1, 2021-03-09:
Yep, thanks for the summary, Dave!

By the way, a lot of the infrastructure needed to formally support 3d-printable exports should be there already; if someone wanted to create a script for it and send a PR that'd be really sweet!

I think it would just require a small tweak to projection_renderer.py to pass in the file extension to use when rendering each individual component (.stl instead of .svg), and then would need a new wrapper script akin to generate_2d.py (it would be simpler though, since you don't need to do any of the post-processing or merging that's done for the SVG files). Since that exports each component individually already, the spacing/layout becomes irrelevant and you can lay out the individual STL files yourself using your plater/slicer of choice.

The only thing that I think would be kind of weird is the engravings, which are exported separately from the body they're engraved onto. That approach wouldn't play nice with an STL export, but the current engravings are also probably too small to be worthwhile on a 3d print, so it may be best to just skip engravings initially to keep things simple.

lastcoolnameleft, 2021-03-11:
Instead of having 3d printed parts like laser-cut parts, I wanted to build an integrated solution that let you toggle flags to render the specific piece you want. (e.g. instead of 4 walls for the frame, render the full frame)

I hope to have it better documented, but here's my attempt at a 3d printed model:
https://github.com/lastcoolnameleft/splitflap/blob/3d-print/3d/splitflap.scad

The changes I made are to add a number of "render_xxx" flags to make it easier to export combined pieces instead of individual parts.  For example setting `render_spool` and `render_spool_motor_wheel` to true will print one side of the spool as one piece and `render_spool_struts` as the other.

I also added `render_frame` and `render_captive_nuts` flags to render the frame as 1 assembled piece.

The issue I hit was that it just added to the code complexity and assembling everything became a lot trickier.  One idea was to have individual pieces split up into separate files similar to how there's a pcb.scad which would make the code more composable.  Then there could be a "laser_cut.scad", "3d_print_frame.scad", etc.

I'm definitely open to ideas.

dmadison, 2021-03-12:
How divergent are you imagining the 3D printable design to be?

If it only differs mildly from the laser-cut design (e.g. hiding captive nuts) then a few flags might be fine, coupled with its own module for all of the parts in 3D-printable orientation. Anything more than that and it might be worth splitting the 3D printed version into its own design/file just to keep things from getting too disorganized. It would probably make more sense to rework the `splitflap.scad` file so that the 2D render is conditional; that way it can be `include`'d in other designs and you can reference off of all variables without having to expose them as functions.

I do think the separate flags for each part is overkill. A script could be used to automate exporting the individual parts, probably by iterating through child objects like the projection renderer.

lastcoolnameleft, 2021-03-12:
Great question.  I initially thought it wouldn't be very divergent.  However, I'm hitting concerns that I don't have an answer to (e.g. If the frame is all 1 piece, how do you fit the spool + gear into the frame.  Currently, I brute force it.)

I'm still learning the repo and poked around the /scripts and it appears that openscad.run() lets you override existing variables to generate STL's.  Is that accurate?

I looked into creating a `render_for_3d_printing()` function which sets all of the appropriate variables and overrides to generate the appropriate pieces, but OpenSCAD variable scoping didn't seem to allow for that.  This is my first OpenSCAD project, so let me know if there's an option I've missed.

scottbez1, 2021-03-12:
Yeah, the python scripts are able to override variables using the `-D` command line option (https://en.wikibooks.org/wiki/OpenSCAD_User_Manual/Using_OpenSCAD_in_a_command_line_environment ), whereas that kind of behavior won't be possible from within another scad file without first refactoring splitflap.scad to wrap more things in high level modules. The global variable situation is not great (but in my defense this was also _my_ first OpenSCAD project :stuck_out_tongue: so I didn't have a great sense of OpenSCAD architectural patterns). It's definitely in need of some refactoring. Unfortunately I can't commit to that myself at the moment, but if someone does take on that heroic task I'd very much appreciate if it's done in small increments and separate from any functionality changes for the sake of reviewability.

That said, like @dmadison mentioned, it's probably worth considering the end goal before getting too deep in the splitflap.scad weeds. The design as it stands today was very much built for laser-cutting, with that assumption baked into nearly every design decision. At a certain point it may make sense to just factor out some of the core dimension calculations (spool dimensions, window size and position relative to the motor, etc) to a library and build the actual pieces up from scratch using just that core library.
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
dmadison, 2021-04-18:
That looks great @KostasDaskalos! If you do need to make any changes, there is a way to export the STLs directly from OpenSCAD. [See my comment earlier in the thread](https://github.com/scottbez1/splitflap/issues/127#issuecomment-792819989).

KostasDaskalos, 2021-04-18:
The only 3D CAD program I know is Fusion 360 ( and I am still learning... ). I am old enough to get into another one ( OpenSCAD ), my brain can not hold that much information any more... Importing STL files to Fusion 360 and working with them is a bit troublesome so I did ...all these steps to import DXF to Fusion 360. Now I can change anything I want and export STL files from Fusion. Tomorrow I will have all pieces printed and assembled ( still needs 5 more time printing... ).
At some point in the future I may take a look at OpenSCAD...

KostasDaskalos, 2021-04-19:
A quick update, as I am still 3D printing one side part:
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
It needs a bit ...sanding around the corners where the pieces press fit but over all I think it is a nice model. It is as well so nice press fitted that actually it can be build without screws!
One piece left. I will test it and I will post the final STL result here!
Have a nice day :)

KostasDaskalos, 2021-04-19:
Done!
Proof Of Concept:
https://www.youtube.com/watch?v=AqFgEZLnIoI
I am sorry for the bad video quality but I do not have a very good phone ... Link for the files is in the description of the video but here it is again:
https://drive.google.com/file/d/1yVeEgPqHvn44Lm4M6I_Hzljlyx13a50h/view?usp=sharing
Some notes regarding the final models:

- Yes some tweaking could be done better so the models do not need sanding but at least the fit is tight! I am pretty sure it can work without screws!
- The body of the spool can be done in one piece with minimal support but I will do it in a future version.
- The holes in the spool wheels seem to be very fragile but they are not! Tried to break one but it is sturdy enough!

Creality Ender 3 V2 slicer settings:

- Layer Height: 1,2
- Extruder temperature: 200
- Bed temperature: 60
- Filament: PLA 1,75

Have fun with it! And **thank you** for the **awesome** design!

Goopinson, 2021-04-21:
Just wondering, does the spool spin smooth enough? Also, were you able to print multiple and connect them as designed?

KostasDaskalos, 2021-04-21:
I am currently in the process of making the electronics. I tried spinning the spool without cards with an Arduino and some hacked up circuit on breadboard and it works fine! I am going to print 3 more and do a 4 digit display. When I do it I will update here with images and a better ( hopefully... ) video!

len0rd, 2023-02-24:
for those coming across this thread looking for a more printer-friendly module case, i ended up consolidating the v0.7 components from 12 pieces to 4 to streamline the print. I used Fusion360 to combine the components since I dont have the time to invest in learning openscad. After a couple iterations everything is working well for me: Here are [the resulting stls](https://www.printables.com/model/407557-split-flap-display-module-case)

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

Ended up down this rabbit hole after accidentally breaking one of my laser-cut pieces. That was easy-enough to replace independently thanks to the easy stl generation scripts! Thanks for the great project

chip-davis, 2023-12-21:
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

This looks great! Any plans to incorporate the inter-connecting? Thanks!

len0rd, 2023-12-21:
@chip-davis no plans at the moment. I’ll take a second look but I didn’t end up needing them for my project. I made a 36 module display and just used the captive front screws to secure all the modules to a piece of ply board. That was rigid enough for me.

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

JHthe4, 2024-10-31:
Hi everyone,

what a great project this is, and a nice DIY alternative to a ready-made solution like the Vestaboard! I'm price-sensitive, so I was wondering if a clear winner has emerged yet between laser cutting the parts and just 3D printing them, and how far this project is with supporting 3D printing out of the box (for enclosures and the flaps themselves), compared to alternatives like https://github.com/dmlambo/SplitFlap . In particular, I like that this project's code and addressing system seems to be much more mature, but I'm wondering about cost differences when looking at a ~60 module display.

Thanks in advance for any insights you can give!

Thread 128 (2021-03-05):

Flaps going to wrong letters (s/w related)

lastcoolnameleft, 2021-03-05:
I've noticed an issue that I've worked really hard to pinpoint and I think might be software related:

To reproduce the issue:
With only 2 modules, in the console type:
```
@
aa
by
yb
```

Expectation:
Both split flaps will go through the full cycle, then to go `aa` then `by` then `yb`.

What happens:
Both split flaps will go through the full cycle, then to go `aa` then `by` then `rb`.

The logs indicate that it should be on `yb`, but the module stops moving past `r`.  The funny thing is if I do `@` after those commands, it goes to `yb`, where I would expect.  I have consistently reproduced this problem.

The reason I don't think this is a mechanical problem is because I swapped which ports the modules were plugged into and was able to reproduce the problem. (e.g. If it was a mechanical problem, then I would have expected the same module to have a problem, but instead it was always module 1).

Here's the debug logs:

```
@VERBOSE: Found home!
VERBOSE: DELTA FLAPS=40
Calculated new expected home 2048.
OLD:us=0, ue=0, m=0
NEW:us=255, ue=2036, m=2060
VERBOSE: DELTA FLAPS=3
Going to flap index 3. Current step is 0. Delta is 154
VERBOSE: Found home!
VERBOSE: DELTA FLAPS=40
Calculated new expected home 2048.
OLD:us=0, ue=0, m=0
NEW:us=255, ue=2036, m=2060
VERBOSE: DELTA FLAPS=3
Going to flap index 3. Current step is 0. Delta is 154
=aa\n
{"type":"move_echo", "dest":"VERBOSE: DELTA FLAPS=38
Going to flap index 1. Current step is 154. Delta is 1946
aVERBOSE: DELTA FLAPS=38
Going to flap index 1. Current step is 154. Delta is 1946
a"}
VERBOSE: Found expected home.VERBOSE: DELTA FLAPS=40
Calculated new expected home 4096.
OLD:us=255, ue=2036, m=2060
NEW:us=2307, ue=4084, m=4108
VERBOSE: Found expected home.VERBOSE: DELTA FLAPS=40
Calculated new expected home 4096.
OLD:us=255, ue=2036, m=2060
NEW:us=2308, ue=4084, m=4108
{"type":"status", "modules":[{"state":"normal", "flap":"a", "count_missed_home":0, "count_unexpected_home":0}, {"state":"normal", "flap":"a", "count_missed_home":0, "count_unexpected_home":0}]}
=by\n
{"type":"move_echo", "dest":"VERBOSE: DELTA FLAPS=1
Going to flap index 2. Current step is 2100. Delta is 51
bVERBOSE: DELTA FLAPS=24
Going to flap index 25. Current step is 2100. Delta is 1228
y"}
{"type":"status", "modules":[{"state":"normal", "flap":"b", "count_missed_home":0, "count_unexpected_home":0}, {"state":"normal", "flap":"y", "count_missed_home":0, "count_unexpected_home":0}]}
=yb\n
{"type":"move_echo", "dest":"VERBOSE: DELTA FLAPS=23
Going to flap index 25. Current step is 2151. Delta is 1177
yVERBOSE: DELTA FLAPS=17
Going to flap index 2. Current step is 3328. Delta is 871
b"}
VERBOSE: Found expected home.VERBOSE: DELTA FLAPS=40
Calculated new expected home 2048.
OLD:us=2307, ue=4084, m=12
NEW:us=260, ue=2036, m=2060
{"type":"status", "modules":[{"state":"normal", "flap":"y", "count_missed_home":0, "count_unexpected_home":0}, {"state":"normal", "flap":"b", "count_missed_home":0, "count_unexpected_home":0}]}
```

I'm interested to know if you're able to reproduce this problem.  Let me know if there's any additional information I can provide to help debug.

scottbez1, 2021-03-05:
After the `=yb` command that ends up at the wrong position, can you send the same `=yb` command again and tell me what the behavior is?

Also, just for my info, what electronics hardware are you using to drive the motors? And if you can, what is the resistance measured between the red and blue wires on the motor connector? (you may have to wait a little while for the measurement to settle after connecting a multimeter)

lastcoolnameleft, 2021-03-05:
If I send the `=yb` command again after the first one, the behavior is that the first modules appears to lose home and then correctly displays `yb`

I am using an Arduino Uno with the board purchased from your Tindie store with the Commit: a1eb737 Date: 2019-01-14 (i.e. no deviation from your ordering guide)

All of my motors are show between 105-108 ohms when I measure between the red and blue wires (I'm colorblind, so I assume you mean the 1st and last wires.  Let me know if I got that incorrect)

Here's the logs from the start:
```
@VERBOSE: Found home!
VERBOSE: DELTA FLAPS=40
Calculated new expected home 2048.
OLD:us=0, ue=0, m=0
NEW:us=255, ue=2036, m=2060
VERBOSE: DELTA FLAPS=25
Going to flap index 25. Current step is 0. Delta is 1280
VERBOSE: Found home!
VERBOSE: DELTA FLAPS=40
Calculated new expected home 2048.
OLD:us=0, ue=0, m=0
NEW:us=255, ue=2036, m=2060
VERBOSE: DELTA FLAPS=2
Going to flap index 2. Current step is 0. Delta is 103
=aa\n
{"type":"move_echo", "dest":"VERBOSE: DELTA FLAPS=16
Going to flap index 1. Current step is 1280. Delta is 820
aVERBOSE: DELTA FLAPS=39
Going to flap index 1. Current step is 103. Delta is 1997
a"}
VERBOSE: Found expected home.VERBOSE: DELTA FLAPS=40
Calculated new expected home 4096.
OLD:us=255, ue=2036, m=2060
NEW:us=2308, ue=4084, m=4108
VERBOSE: Missed expected home! At 2060. Expected between 2036 and 2060.
VERBOSE: Found home!
VERBOSE: DELTA FLAPS=40
Calculated new expected home 2048.
OLD:us=0, ue=0, m=0
NEW:us=255, ue=2036, m=2060
VERBOSE: DELTA FLAPS=1
Going to flap index 1. Current step is 0. Delta is 52
{"type":"status", "modules":[{"state":"normal", "flap":"a", "count_missed_home":0, "count_unexpected_home":0}, {"state":"normal", "flap":"a", "count_missed_home":1, "count_unexpected_home":0}]}
=by\n
{"type":"move_echo", "dest":"VERBOSE: DELTA FLAPS=1
Going to flap index 2. Current step is 2100. Delta is 51
bVERBOSE: DELTA FLAPS=24
Going to flap index 25. Current step is 52. Delta is 1228
y"}
{"type":"status", "modules":[{"state":"normal", "flap":"b", "count_missed_home":0, "count_unexpected_home":0}, {"state":"normal", "flap":"y", "count_missed_home":1, "count_unexpected_home":0}]}
=yb\n
{"type":"move_echo", "dest":"VERBOSE: DELTA FLAPS=23
Going to flap index 25. Current step is 2151. Delta is 1177
yVERBOSE: DELTA FLAPS=17
Going to flap index 2. Current step is 1280. Delta is 871
b"}
VERBOSE: Found expected home.VERBOSE: DELTA FLAPS=40
Calculated new expected home 4096.
OLD:us=255, ue=2036, m=2060
NEW:us=2308, ue=4084, m=4108
{"type":"status", "modules":[{"state":"normal", "flap":"y", "count_missed_home":0, "count_unexpected_home":0}, {"state":"normal", "flap":"b", "count_missed_home":1, "count_unexpected_home":0}]}
=yb\n
{"type":"move_echo", "dest":"VERBOSE: DELTA FLAPS=40
Going to flap index 25. Current step is 3328. Delta is 2048
yVERBOSE: DELTA FLAPS=40
Going to flap index 2. Current step is 2151. Delta is 2048
b"}
VERBOSE: Missed expected home! At 12. Expected between 4084 and 12.
VERBOSE: Found home!
VERBOSE: DELTA FLAPS=40
Calculated new expected home 2048.
OLD:us=0, ue=0, m=0
NEW:us=255, ue=2036, m=2060
VERBOSE: DELTA FLAPS=25
Going to flap index 25. Current step is 0. Delta is 1280
VERBOSE: Missed expected home! At 12. Expected between 4084 and 12.
VERBOSE: Found home!
VERBOSE: DELTA FLAPS=40
Calculated new expected home 2048.
OLD:us=0, ue=0, m=0
NEW:us=255, ue=2036, m=2060
VERBOSE: DELTA FLAPS=2
Going to flap index 2. Current step is 0. Delta is 103
{"type":"status", "modules":[{"state":"normal", "flap":"y", "count_missed_home":1, "count_unexpected_home":0}, {"state":"normal", "flap":"b", "count_missed_home":2, "count_unexpected_home":0}]}
```

scottbez1, 2021-03-06:
I'm not able to reproduce this.

I would start debugging by setting `HOME_CALIBRATION_ENABLED` to false in config.h https://github.com/scottbez1/splitflap/blob/095603151c19d6603472c50c959f4c5708cc02f1/arduino/splitflap/Splitflap/config.h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

This will eliminate any potential sensor issues influencing the behavior.

Now you can just repeatedly send `=  \n` (equal, space, space, newline) and each time both modules should complete a full revolution, ending on the same letter they were on when the Arduino started. Do this a bunch of times (at least 10 in a row)

There are two things you might notice:
- if a module stops spinning very early after just one or two rotations (and hums/vibrates while stopped until the other module stops moving too), this suggests a mechanical/torque limit. If that is the case, the best solution is probably to slow down the max speed (since torque decreases at higher speeds). You can do this by modifying generate_acceleration.py to set a higher minimum period (maybe 1500 instead of the default 1200). https://github.com/scottbez1/splitflap/blob/095603151c19d6603472c50c959f4c5708cc02f1/arduino/splitflap/Splitflap/src/generate_acceleration.py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 Then run that script, which updates acceleration.h, and then re-upload the code to the Arduino (if using the Arduino IDE, make sure to close it while running the script and then reopen it)
- The other possibility is that after many rotations you notice the module is slowly drifting from the correct location, most likely rotating slightly too far each time. This does not sound like it's the case for you, but this would indicate that the motor has a different gear ratio than the expected 64:1. There are some comments about changing the gear ratio in splitflap_module.h - https://github.com/scottbez1/splitflap/blob/095603151c19d6603472c50c959f4c5708cc02f1/arduino/splitflap/Splitflap/src/splitflap_module.h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

If something else happens, can you record a video of the test and link to it here? Thanks

scottbez1, 2021-03-21:
Any luck tracking down the issue @lastcoolnameleft ?

lastcoolnameleft, 2021-03-23:
Unfortunately no.  I think that even though I put in extra due diligence to make sure it wasn't an issue on my side, that it ultimately was PEBKAC.  I haven't spent much time with it as I'm anxiously awaiting the larger controller board to spend my next chunk of time on.

I'll close for now and re-open in case I encounter the issue again.  Thanks for your investigation.

Closed 2021-03-23.

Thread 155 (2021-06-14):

Consider breaking flap dimension change?

scottbez1, 2021-06-14:
The flap dimensions have always been "wrong" though they generally work ok. This issue is to track comments/considerations around fixing those dimensions, which would be a breaking change (and a potentially confusing one, given the changes will likely be around 0.5mm in aggregate).

Historically it was believed that Ponoko sold 3.2mm thick MDF (because that's what their website incorrectly stated when this project started) so the notches on the flaps were designed to be 3.2mm wide to match. Even if the MDF was actually nominally 3.2mm thick, it was a mistake to set the notches to that exact width, as any variability in thickness would mean that the flap edges and flap pins could extend _past_ the spool where they can more easily get caught on the sides of the front window.

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

However, since the MDF and acrylic are actually both 3mm nominal thickness, this means that an accurately cut flap can stick out by 0.2mm on either side of the spool (or more, if the real material thickness is below nominal thickness, such as Elecrow wood which is closer to 2.8mm in my experience).

The challenge with fixing this is that it will require both a flap revision and enclosure revision, and users will have to be _very_ careful to make sure they are using matching revisions as they will look nearly identical but will not be compatible. It also requires ordering a new tool for the custom flaps I sell (~$120 one-time fee) and maintaining inventory of both variants for a while; there is also an ongoing risk that the supplier may accidentally use the wrong tool for future orders due to the visual similarity, or that I may accidentally pack the wrong flaps when fulfilling orders.

The major question is whether it's worth dealing with the hassle of fixing this at this point considering the potential for confusion and complication with inventory and compatibility. As long as the spool is well-centered in the window I have not personally had issues with the flaps catching on the window since there is built-in tolerance/slop between the spool and window, but others have occasionally reported flaps getting caught (though it isn't 100% clear that this was the reason for that). Basically it's unclear if this theoretical problem is actually a critical enough issue in practice to be worth fixing, especially considering the practical complexity of fixing it.

An alternative "fix" would be to officially recommend using shim washers to maintain spacing if needed, and potentially increase the gap between the spool and window sides a bit, which would not be a breaking change and has no compatibility/inventory-control complications.

dmadison, 2021-06-14:
My vote is to leave it as is.

Aside from the manufacturing headaches of trying to maintain two versions of the flaps, I think the concern for the extra 0.2 mm of the 'pins' is misplaced. In my experience the flaps don't get stuck because the pins hit the side of the enclosure, they get stuck (if they get stuck) because the flap "twists" in the spool holes along Y, so the top corners of the flap hit the side of the enclosure. Keeping the spool slop loose is far easier than trying to tighten up all of the tolernaces with the laser-cut enclosure.

With the current version on master I've had no issues with the 3.2 mm flaps getting stuck in my 3.0 mm enclosures, though I did need to back the acceleration off for some of the motors (8ab30be is a similar change).

It's also worth bearing in mind that manufacturers come and go, and with the changes of #93 the design should now be flexible to varying thicknesses (including 3.2 mm). For Yanks with access to 1/8" material and a laser-cutter the 3.2 mm flaps are still perfect.

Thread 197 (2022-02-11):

Loose spool

gorwah, 2022-02-11:
Fitting for spool on side closest to motor is very loose. What would you suggest to tighten? Glue? Tape?

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

gorwah, 2022-02-11:
A couple of pieces of tape solved it
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

Closed 2022-02-11.

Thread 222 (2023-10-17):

Loopback ERROR. Set output 0 but read incorrect value at input 0

brandonfake69, 2023-10-17:
I'm just setting one up and trying to Upload and Monitor. I get the following error:

```
{"type":"init", "num_modules":6}
{"msg": "Loopback ERROR. Set output 0 but read incorrect value at input 0", "type": "log"}
{"msg": "Loopback ERROR. Set output 1 but read incorrect value at input 1", "type": "log"}
f~�f~��x�x������x�x~`怘�怘���~�f�f�~f������f�f`ff�������`�~f�x�ff�f`�f�f`�����f����`f�������xf�~��f��~���f�ff~fxff�������fx�~���fx�~��`�fx�~�����fx�~����`�fx�~��~�fx�~�������`fx�`�������������x��x�~�������x��xx�xx�����f���怘�����x��xx�xx�������f�����`�������x������f�������x`�������x����f�����x����f��`��f���

{"type":"init", "num_modules":6}
{"msg": "Loopback ERROR. Set output 0 but read incorrect value at input 0", "type": "log"}
{"msg": "Loopback ERROR. Set output 1 but read incorrect value at input 1", "type": "log"}
```

I have 1 chainlink driver connected but and I'm not really sure where to go from here.

Thanks!

brandonfake69, 2023-10-17:
I have solid red LEDs on all 6 of the channels

scottbez1, 2023-10-17:
Most commonly this will occur with an incomplete crimped IDC connector, or with potential incomplete or bridged solder joints on the connectors on the PCBs. I would recommend starting there to see if anything stands out as a potential issue; if not, or if you're unsure, sending a high res photo of the whole setup (ESP32 and Chainlink driver), as well as any close-ups of solder joints you're unsure about can often be helpful to spot things.

Closed 2023-10-27.

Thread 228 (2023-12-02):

LILYGO ESP32 doesn't show up as device despite drivers on MacBook with USC-C ports

JoshuaPerk, 2023-12-02:
Wanted to document an issue I'm troubleshooting. It's unrelated to this library so I don't expect community support but wanted the closed issue to potentially help future makers (once I diagnose the problem myself).

Despite installing a variety of drivers ([CH34XSER](https://learn.adafruit.com/how-to-install-drivers-for-wch-usb-to-serial-chips-ch9102f-ch9102/mac-driver-installation), [CH341SER](https://www.wch.cn/downloads/CH341SER_MAC_ZIP.html) — using both `.pkg` and `.DMG` files and manually adding Mac's Rosetta to support drivers with older architecture) I've been unable to get the ESP-32 to show up as a device.

I'm on 2021 MacBook Pro with an M1 Pro running Ventura 13.4. My machine _only_ has support for USB-C ports.

I _suspect_ this might be related to [some of the issues](https://www.reddit.com/r/esp32/comments/x7odev/esp32_devkit_usbc_boards_not_working_with_usbc/) folks have seen where they're unable to go directly from USC-C to USB-C.

I've attempted 3 different USC-C to USB-C cables (all of which support data and work when a device such as my iPhone are plugged into it).

I've also attempted to use 1 USB-A to USC-C cable that's plugged into a USB-C dongle (with multiple USB-A 3.0) ports (+ ethernet, HDMI, SD card, etc.). This also doesn't work, despite that same setup working if I plug my iPhone into it.

I placed an order for a new [USB-A to USB-C cable](https://www.amazon.com/gp/product/B0794M53HQ/ref=ppx_yo_dt_b_asin_title_o00_s01?ie=UTF8&th=1) with a [USB-A to USB-C dongle](https://www.amazon.com/gp/product/B07CVX3516/ref=ppx_yo_dt_b_asin_title_o00_s01?ie=UTF8&psc=1).

I'll update this (and close it) once I resolve it.

P.S. Received my hardware order from @scottbez1 and these boards are _beautiful_. Well done! 🔥

JoshuaPerk, 2023-12-02:
Ah, interesting. I ordered 2x TTGO boards and one of them shows up just fine with a USB-C cable (totally negating my theory above).

I will try to diagnose why the first board is unresponsive on the port.

JoshuaPerk, 2023-12-02:
Seems to be a bad USB chip - will probably just order a new one unless anyone knows how to reset the firmware without being a recognized device.

scottbez1, 2023-12-02:
Unfortunately the Lilygo T-Display board has an error in their design, which can make it fail to enumerate correctly with a USB-C to C cable -- one of the 2 CC lines is not connected to the correct USB-C pin, and they are only using a single CC resistor.

This can make the USB-C connector directional, and sometimes may only work when the connector is plugged in one way and not the other :disappointed:

If you've tried the USB-A to C plug, ideally with a USB 2.0 port rather than 3.0 port on your computer, and tried plugging the USB-C end into the T-Display both ways and it's still not enumerating (but the other T-Display works), **please send me a message on Etsy and I can process a refund/replacement for that one defective T-Display**.

For USB 2.0 on a type C connector, it's typical to connect 2 5.1k resistors, one to each of the CC1/CC2 pins, in order for the device to be detected and for it to receive power at 5V. The T-Display only has a single resistor, and they've connected it to A5 (which is correct) and also B8 (which is incorrect for 2 reasons - the second CC pin should not share a resistor, and the second CC pin is B5, not B8).

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

Any future revision to the controller portion of this project will definitely use a better module... The T-Display was one of the better modules for its time, but there are better options available for new designs today.

JoshuaPerk, 2023-12-05:
@scottbez1 Here's my attempt at a (failed) clean install: https://video.drift.com/v/abkLtL8scZirYP9gRbX3qmaZcCwSctW1wcY6wbv5uwOzM/

JoshuaPerk, 2023-12-05:
Resolved: https://video.drift.com/v/abwDzmH8Rqo8JmEof6nIEin00uRlwJB8WlQewGrAaFs/
Discord thread: https://discord.com/channels/521805668735385606/521806401807450115/1181404579502510130

Closed 2023-12-05.

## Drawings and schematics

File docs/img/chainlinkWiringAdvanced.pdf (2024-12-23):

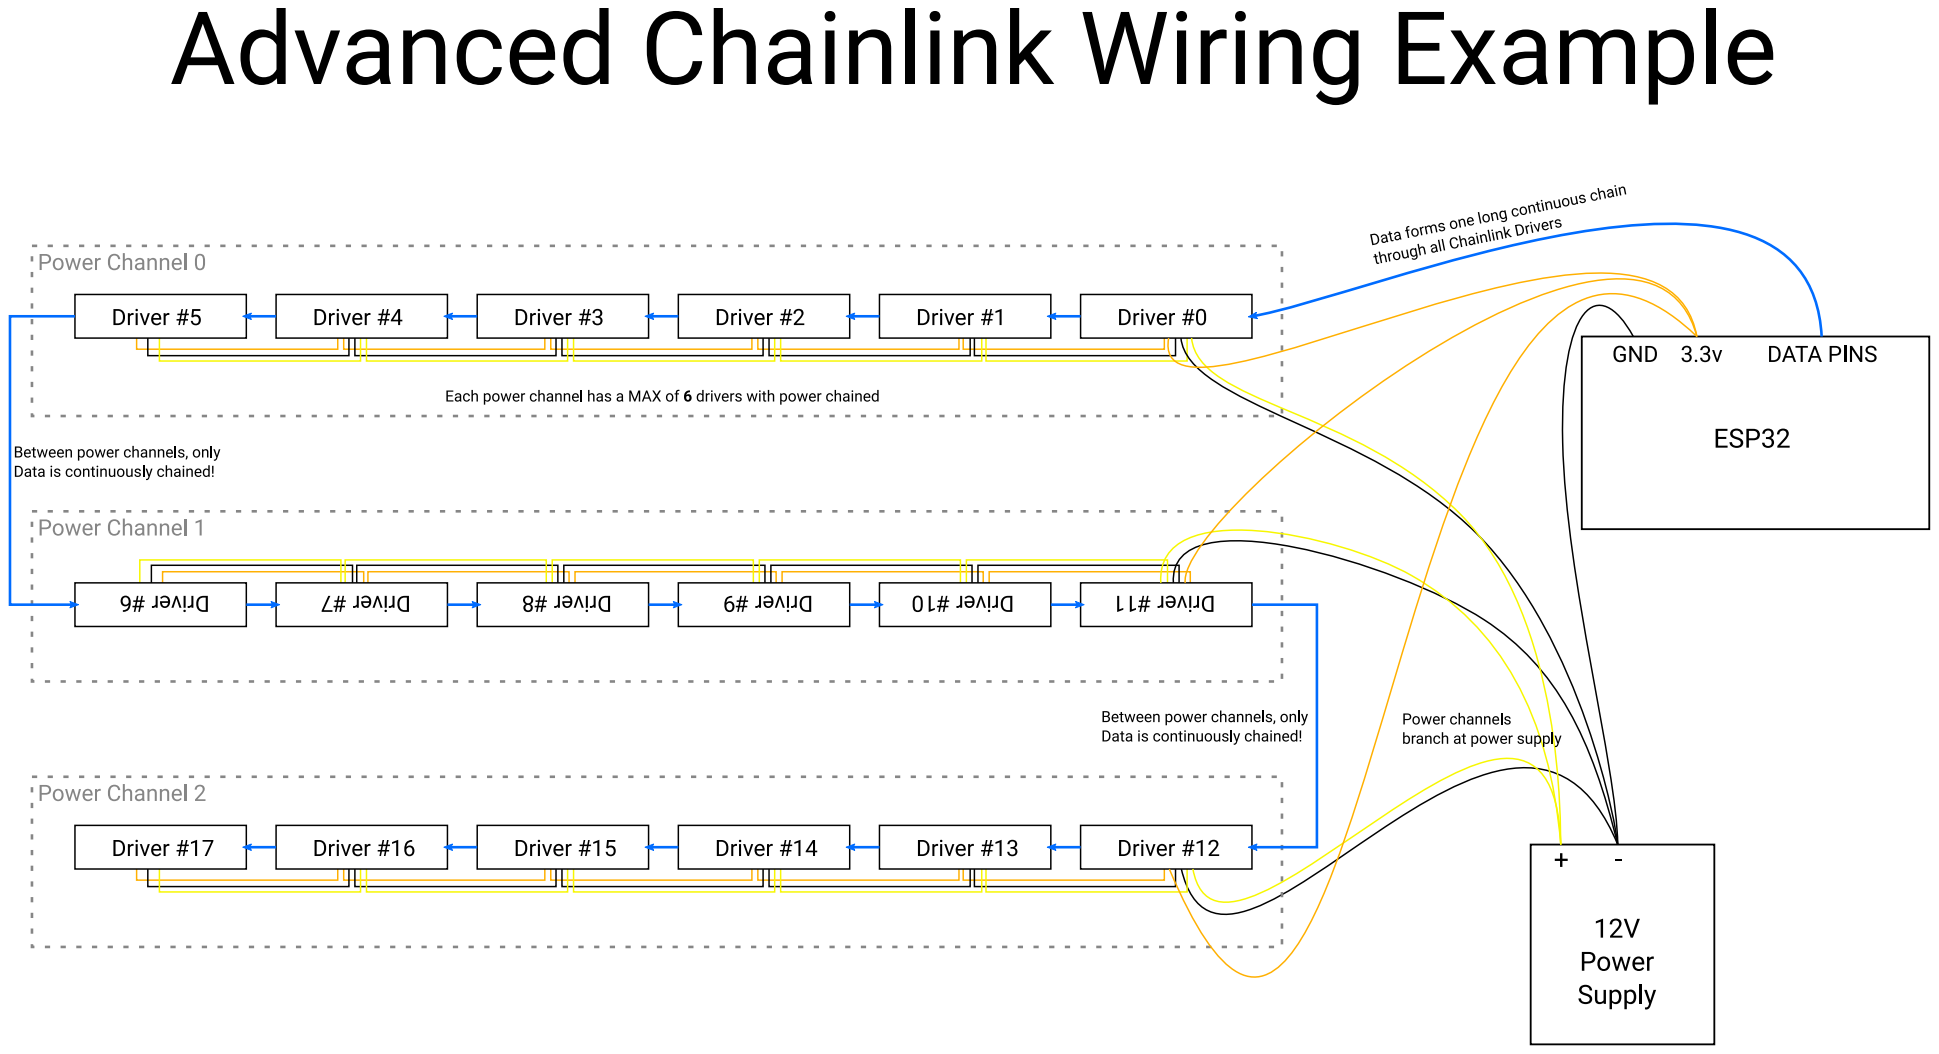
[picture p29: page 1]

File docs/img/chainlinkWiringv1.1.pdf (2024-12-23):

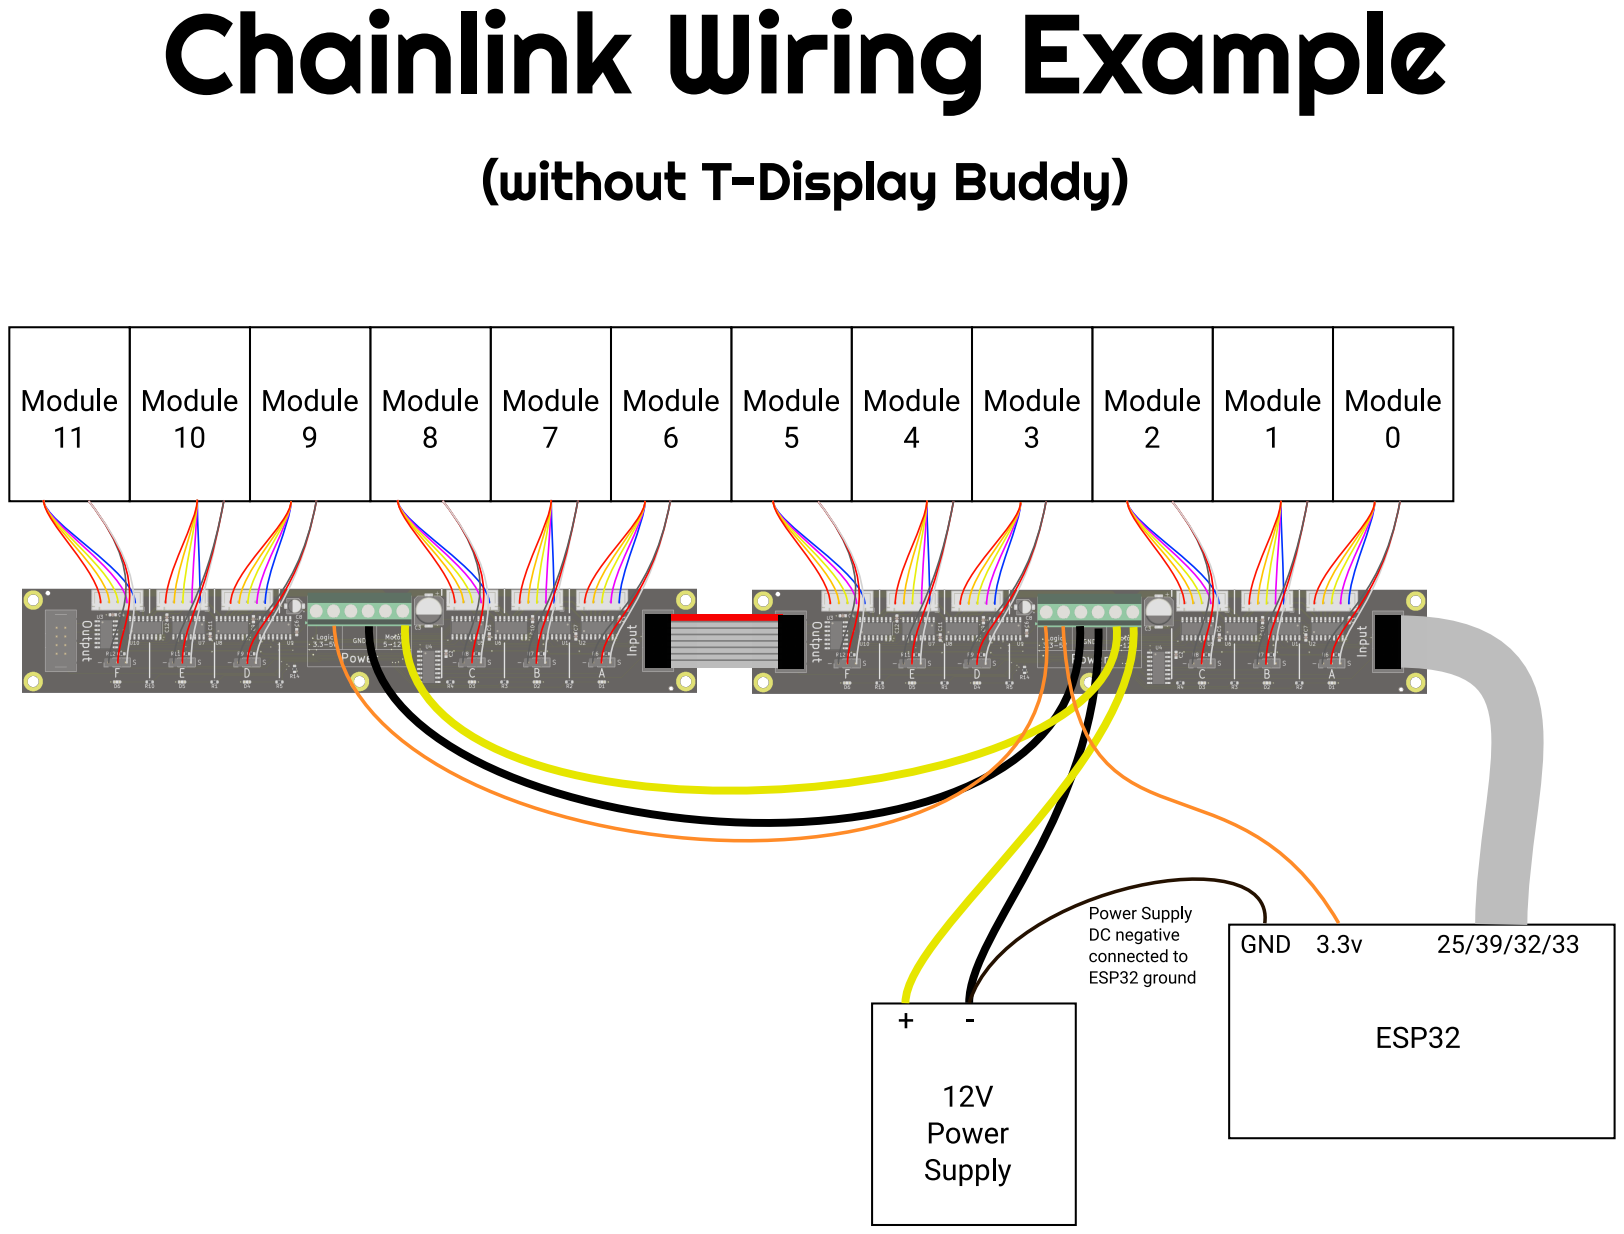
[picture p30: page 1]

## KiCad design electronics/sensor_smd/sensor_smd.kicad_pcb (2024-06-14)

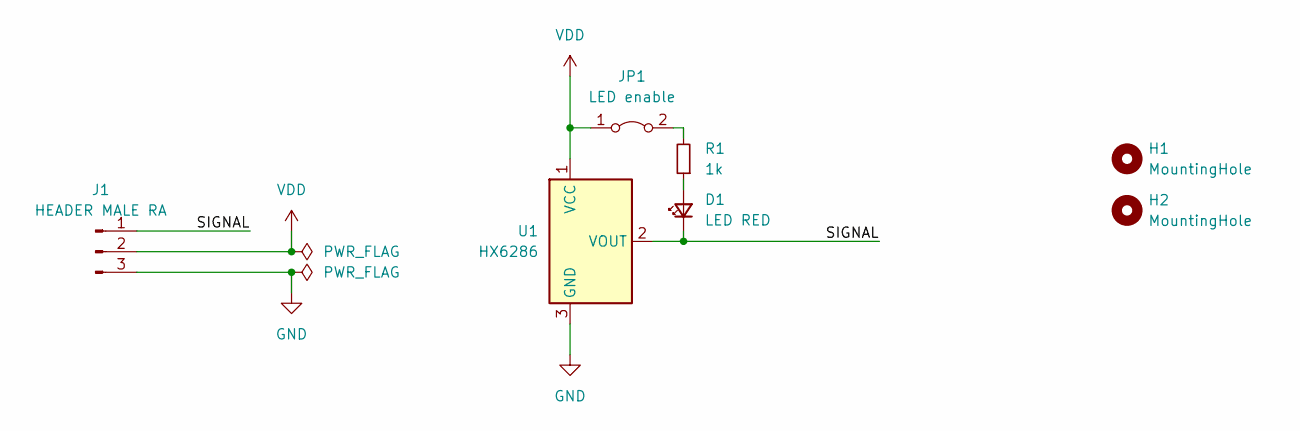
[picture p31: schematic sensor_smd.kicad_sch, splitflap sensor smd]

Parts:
D1: LED RED; LED_0603_1608Metric; LCSC C2286
H1: MountingHole; MountingHole_4.3mm_M4_ISO7380
H2: MountingHole; hole_9.4
J1: HEADER MALE RA; header_3_smd
JP1: LED enable; SolderJumper-2_P1.3mm_Bridged_Pad1.0x1.5mm
R1: 1k; R_0603_1608Metric; LCSC C21190
U1: HX6286; SOT-23W; LCSC C495736

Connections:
/SIGNAL: D1.1 (K), J1.1, U1.2 (VOUT)
GND: J1.3, U1.3 (GND)
unnamed: D1.2 (A), R1.1
unnamed: JP1.2 (B), R1.2
VDD: J1.2, JP1.1 (A), U1.1 (VCC)

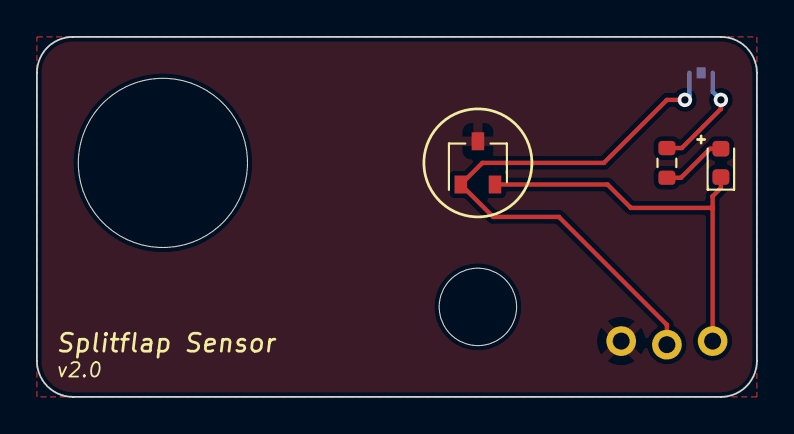
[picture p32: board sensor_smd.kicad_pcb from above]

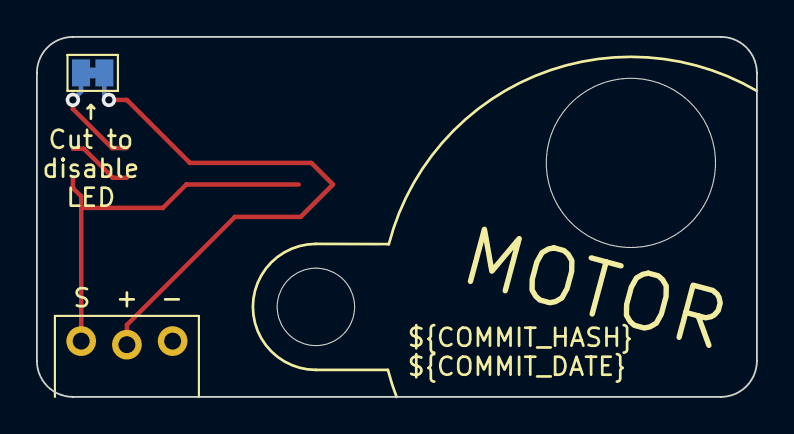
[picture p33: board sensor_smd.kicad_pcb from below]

Board: 2 copper layers, 40.0 x 20.0 mm, 7 parts (2 on the bottom side), 5 nets.

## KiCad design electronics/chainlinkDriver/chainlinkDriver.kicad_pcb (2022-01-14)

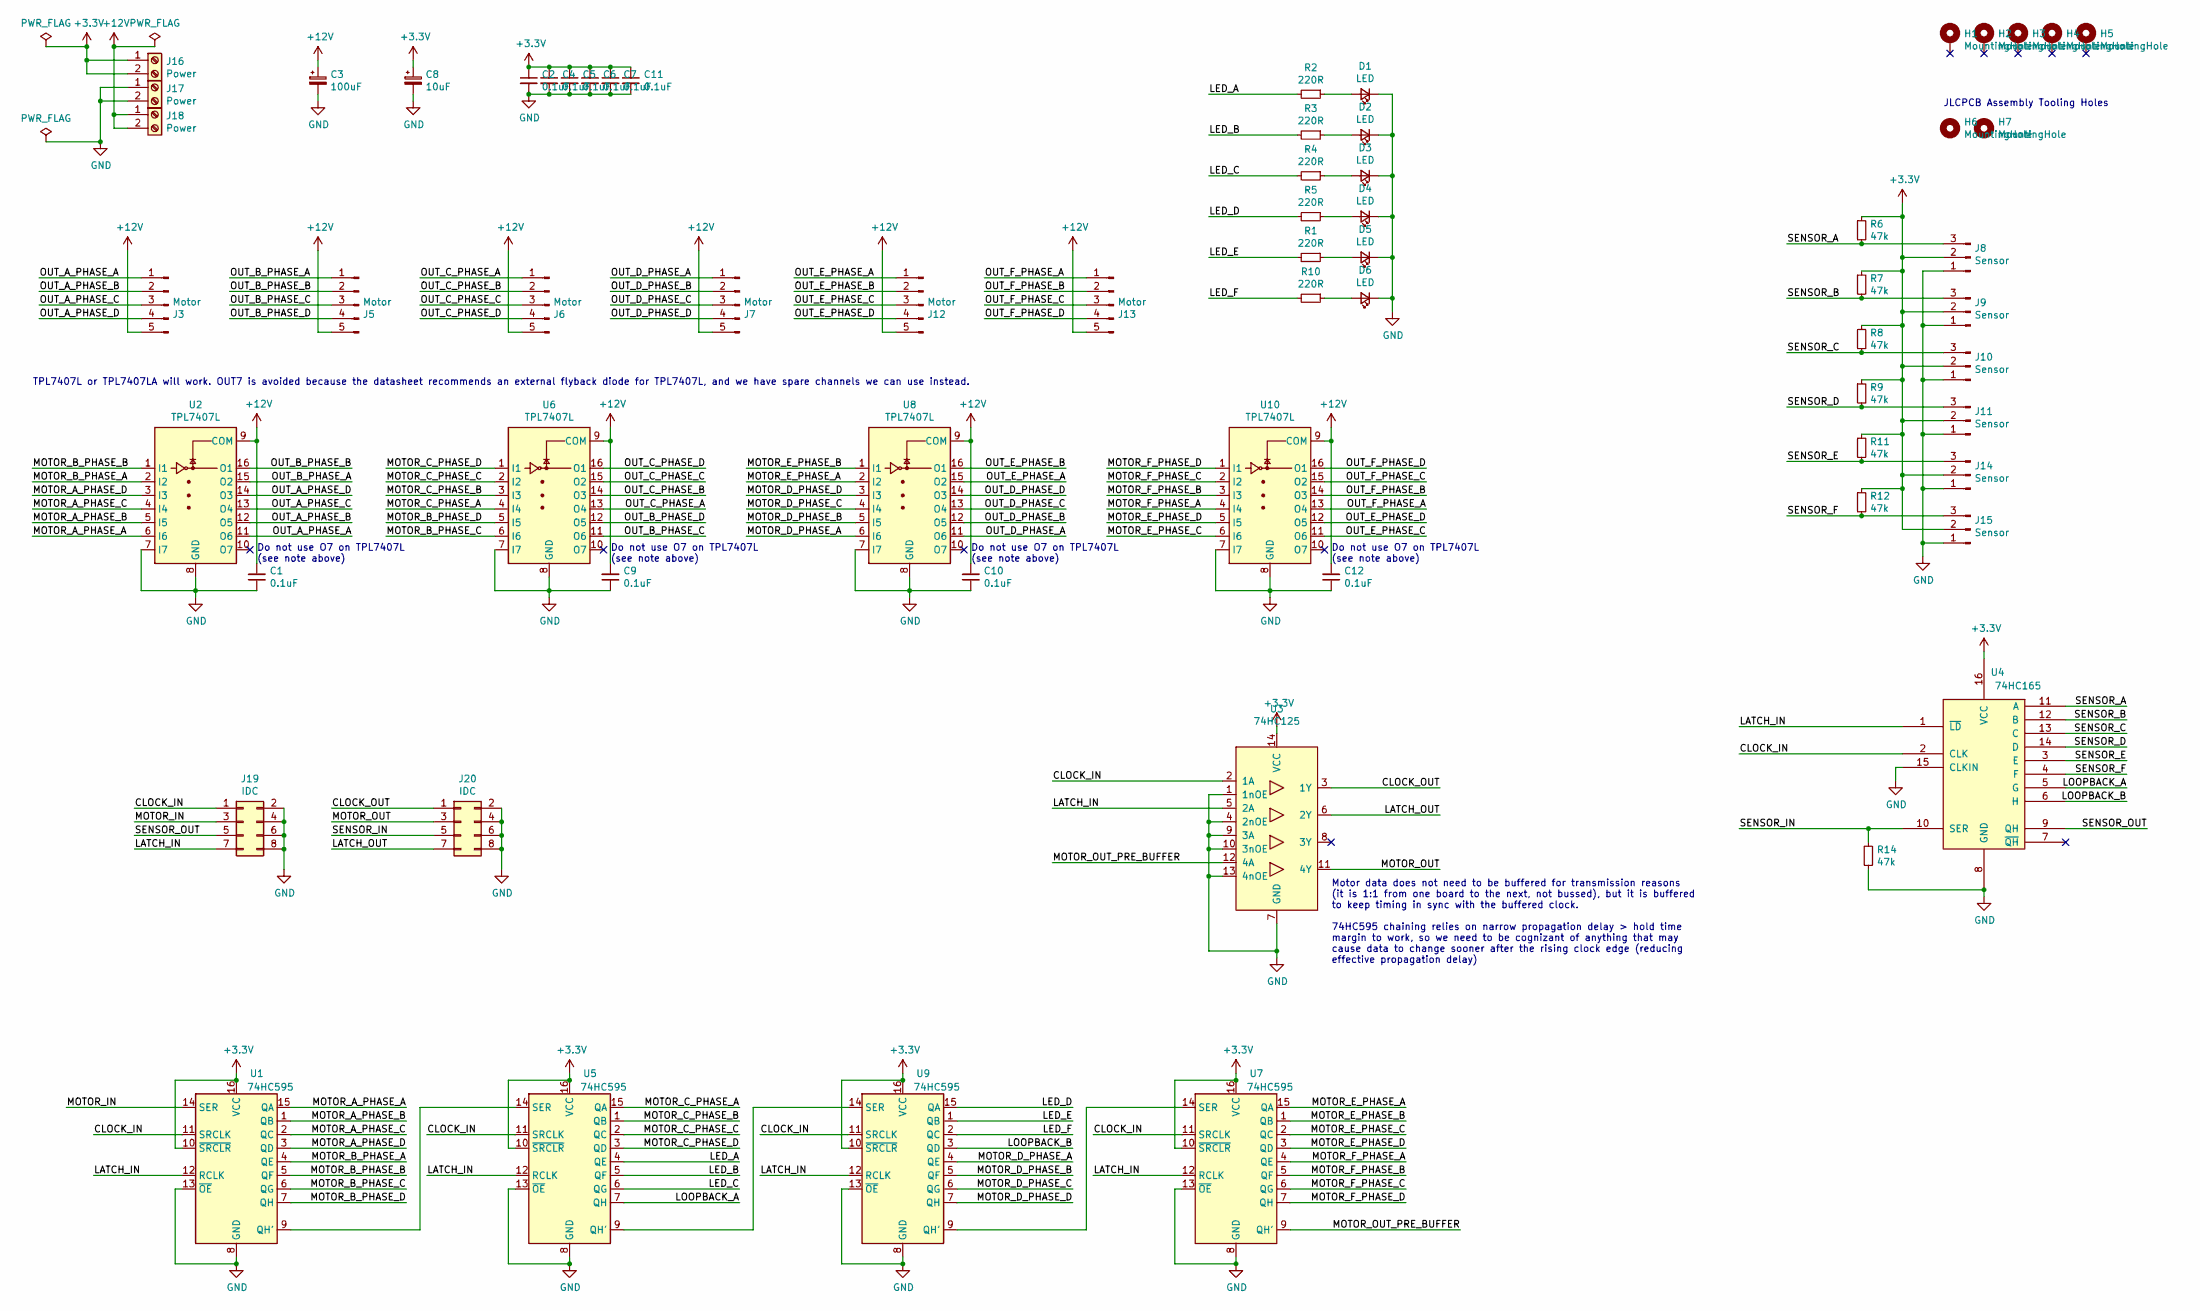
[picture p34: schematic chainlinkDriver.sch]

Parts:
C1, C2, C4, C5, C6, C7, C9, C10, C11, C12: 0.1uF; C_0603_1608Metric; LCSC C14663
C3: 100uF; CP_Elec_8x10; LCSC C176665
C8: 10uF; CP_Elec_4x5.3; LCSC C134721
D1, D2, D3, D4, D5, D6: LED; LED_0603_1608Metric_Silkscreen; LCSC C2286
H1, H2, H3, H4, H5: MountingHole; MountingHole_3.2mm_M3_ISO7380_Pad
H6, H7: MountingHole; AssemblyToolingHole
J3, J5, J6, J7, J12, J13: Motor; JST_XH_B5B-XH-A_1x05_P2.50mm_Vertical
J8, J9, J10, J11, J14, J15: Sensor; PinHeader_1x03_P2.54mm_Vertical
J16, J17, J18: Power; Generic-5.08-2P; LCSC C8465
J19, J20: IDC; IDC-Header_2x04_P2.54mm_Vertical
R1, R2, R3, R4, R5, R10: 220R; R_0603_1608Metric; LCSC C22962
R6, R7, R8, R9, R11, R12, R14: 47k; R_0603_1608Metric; LCSC C25819
U1, U5, U7, U9: 74HC595; SOIC-16_3.9x9.9mm_P1.27mm_silk; LCSC C5947
U2, U6, U8, U10: TPL7407L; SOIC-16_3.9x9.9mm_P1.27mm_silk; LCSC C139663
U3: 74HC125; SOIC-14_3.9x8.7mm_P1.27mm_silk; LCSC C5598
U4: 74HC165; SOIC-16_3.9x9.9mm_P1.27mm_silk; LCSC C5613

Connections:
+3V3: C2.1, C4.1, C5.1, C6.1, C7.1, C8.1, C11.1, J8.2, J9.2, J10.2, J11.2, J14.2, J15.2, J16.1, J16.2, R6.1, R7.1, R8.1, R9.1, R11.1, R12.1, U1.10 (~SRCLR), U1.16 (VCC), U3.14 (VCC), U4.16 (VCC), U5.10 (~SRCLR), U5.16 (VCC), U7.10 (~SRCLR), U7.16 (VCC), U9.10 (~SRCLR), U9.16 (VCC)
+12V: C1.2, C3.1, C9.2, C10.2, C12.2, J3.5, J5.5, J6.5, J7.5, J12.5, J13.5, J18.1, J18.2, U2.9 (COM), U6.9 (COM), U8.9 (COM), U10.9 (COM)
/CLOCK_IN: J19.1, U1.11 (SRCLK), U3.2 (1A), U4.2 (CLK), U5.11 (SRCLK), U7.11 (SRCLK), U9.11 (SRCLK)
/CLOCK_OUT: J20.1, U3.3 (1Y)
/LATCH_IN: J19.7, U1.12 (RCLK), U3.5 (2A), U4.1 (~LD), U5.12 (RCLK), U7.12 (RCLK), U9.12 (RCLK)
/LATCH_OUT: J20.7, U3.6 (2Y)
/LED_A: R2.2, U5.4 (QE)
/LED_B: R3.2, U5.5 (QF)
/LED_C: R4.2, U5.6 (QG)
/LED_D: R5.2, U9.15 (QA)
/LED_E: R1.2, U9.1 (QB)
/LED_F: R10.2, U9.2 (QC)
/LOOPBACK_A: U4.5 (G), U5.7 (QH)
/LOOPBACK_B: U4.6 (H), U9.3 (QD)
/MOTOR_A_PHASE_A: U1.15 (QA), U2.6 (I6)
/MOTOR_A_PHASE_B: U1.1 (QB), U2.5 (I5)
/MOTOR_A_PHASE_C: U1.2 (QC), U2.4 (I4)
/MOTOR_A_PHASE_D: U1.3 (QD), U2.3 (I3)
/MOTOR_B_PHASE_A: U1.4 (QE), U2.2 (I2)
/MOTOR_B_PHASE_B: U1.5 (QF), U2.1 (I1)
/MOTOR_B_PHASE_C: U1.6 (QG), U6.6 (I6)
/MOTOR_B_PHASE_D: U1.7 (QH), U6.5 (I5)
/MOTOR_C_PHASE_A: U5.15 (QA), U6.4 (I4)
/MOTOR_C_PHASE_B: U5.1 (QB), U6.3 (I3)
/MOTOR_C_PHASE_C: U5.2 (QC), U6.2 (I2)
/MOTOR_C_PHASE_D: U5.3 (QD), U6.1 (I1)
/MOTOR_D_PHASE_A: U8.6 (I6), U9.4 (QE)
/MOTOR_D_PHASE_B: U8.5 (I5), U9.5 (QF)
/MOTOR_D_PHASE_C: U8.4 (I4), U9.6 (QG)
/MOTOR_D_PHASE_D: U8.3 (I3), U9.7 (QH)
/MOTOR_E_PHASE_A: U7.15 (QA), U8.2 (I2)
/MOTOR_E_PHASE_B: U7.1 (QB), U8.1 (I1)
/MOTOR_E_PHASE_C: U7.2 (QC), U10.6 (I6)
/MOTOR_E_PHASE_D: U7.3 (QD), U10.5 (I5)
/MOTOR_F_PHASE_A: U7.4 (QE), U10.4 (I4)
/MOTOR_F_PHASE_B: U7.5 (QF), U10.3 (I3)
/MOTOR_F_PHASE_C: U7.6 (QG), U10.2 (I2)
/MOTOR_F_PHASE_D: U7.7 (QH), U10.1 (I1)
/MOTOR_IN: J19.3, U1.14 (SER)
/MOTOR_OUT: J20.3, U3.11 (4Y)
/MOTOR_OUT_PRE_BUFFER: U3.12 (4A), U7.9 (QH')
/OUT_A_PHASE_A: J3.1, U2.11 (O6)
/OUT_A_PHASE_B: J3.2, U2.12 (O5)
/OUT_A_PHASE_C: J3.3, U2.13 (O4)
/OUT_A_PHASE_D: J3.4, U2.14 (O3)
/OUT_B_PHASE_A: J5.1, U2.15 (O2)
/OUT_B_PHASE_B: J5.2, U2.16 (O1)
/OUT_B_PHASE_C: J5.3, U6.11 (O6)
/OUT_B_PHASE_D: J5.4, U6.12 (O5)
/OUT_C_PHASE_A: J6.1, U6.13 (O4)
/OUT_C_PHASE_B: J6.2, U6.14 (O3)
/OUT_C_PHASE_C: J6.3, U6.15 (O2)
/OUT_C_PHASE_D: J6.4, U6.16 (O1)
/OUT_D_PHASE_A: J7.1, U8.11 (O6)
/OUT_D_PHASE_B: J7.2, U8.12 (O5)
/OUT_D_PHASE_C: J7.3, U8.13 (O4)
/OUT_D_PHASE_D: J7.4, U8.14 (O3)
/OUT_E_PHASE_A: J12.1, U8.15 (O2)
/OUT_E_PHASE_B: J12.2, U8.16 (O1)
/OUT_E_PHASE_C: J12.3, U10.11 (O6)
/OUT_E_PHASE_D: J12.4, U10.12 (O5)
/OUT_F_PHASE_A: J13.1, U10.13 (O4)
/OUT_F_PHASE_B: J13.2, U10.14 (O3)
/OUT_F_PHASE_C: J13.3, U10.15 (O2)
/OUT_F_PHASE_D: J13.4, U10.16 (O1)
/SENSOR_A: J8.3, R6.2, U4.11 (A)
/SENSOR_B: J9.3, R7.2, U4.12 (B)
/SENSOR_C: J10.3, R8.2, U4.13 (C)
/SENSOR_D: J11.3, R9.2, U4.14 (D)
/SENSOR_E: J14.3, R11.2, U4.3 (E)
/SENSOR_F: J15.3, R12.2, U4.4 (F)
/SENSOR_IN: J20.5, R14.1, U4.10 (SER)
/SENSOR_OUT: J19.5, U4.9 (QH)
GND: C1.1, C2.2, C3.2, C4.2, C5.2, C6.2, C7.2, C8.2, C9.1, C10.1, C11.2, C12.1, D1.1 (K), D2.1 (K), D3.1 (K), D4.1 (K), D5.1 (K), D6.1 (K), J8.1, J9.1, J10.1, J11.1, J14.1, J15.1, J17.1, J17.2, J19.2, J19.4, J19.6, J19.8, J20.2, J20.4, J20.6, J20.8, R14.2, U1.8 (GND), U1.13 (~OE), U2.7 (I7), U2.8 (GND), U3.1 (1nOE), U3.4 (2nOE), U3.7 (GND), U3.9 (3A), U3.10 (3nOE), U3.13 (4nOE), U4.8 (GND), U4.15 (CLKIN), U5.8 (GND), U5.13 (~OE), U6.7 (I7), U6.8 (GND), U7.8 (GND), U7.13 (~OE), U8.7 (I7), U8.8 (GND), U9.8 (GND), U9.13 (~OE), U10.7 (I7), U10.8 (GND)
unnamed: D1.2 (A), R2.1
unnamed: D2.2 (A), R3.1
unnamed: D3.2 (A), R4.1
unnamed: D4.2 (A), R5.1
unnamed: D5.2 (A), R1.1
unnamed: D6.2 (A), R10.1
unnamed: U1.9 (QH'), U5.14 (SER)
unnamed: U5.9 (QH'), U9.14 (SER)
unnamed: U7.14 (SER), U9.9 (QH')

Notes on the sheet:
JLCPCB Assembly Tooling Holes
TPL7407L or TPL7407LA will work. OUT7 is avoided because the datasheet recommends an external flyback diode for TPL7407L, and we have spare channels we can use instead.
Do not use O7 on TPL7407L (see note above)
Motor data does not need to be buffered for transmission reasons (it is 1:1 from one board to the next, not bussed), but it is buffered to keep timing in sync with the buffered clock. 74HC595 chaining relies on narrow propagation delay > hold time margin to work, so we need to be cognizant of anyth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

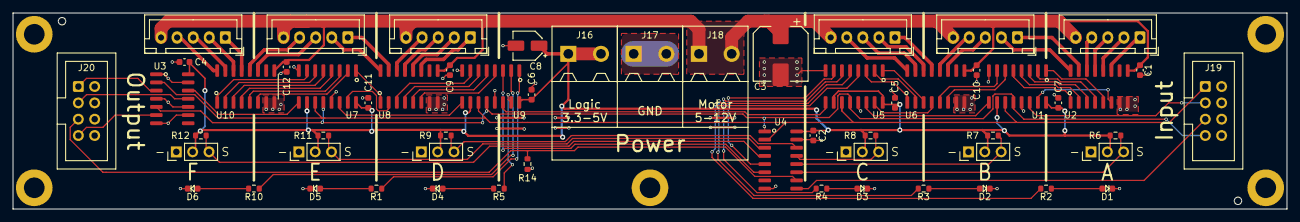
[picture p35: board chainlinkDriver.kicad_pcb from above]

Board: 2 copper layers, 198.1 x 30.5 mm, 65 parts (0 on the bottom side), 83 nets.

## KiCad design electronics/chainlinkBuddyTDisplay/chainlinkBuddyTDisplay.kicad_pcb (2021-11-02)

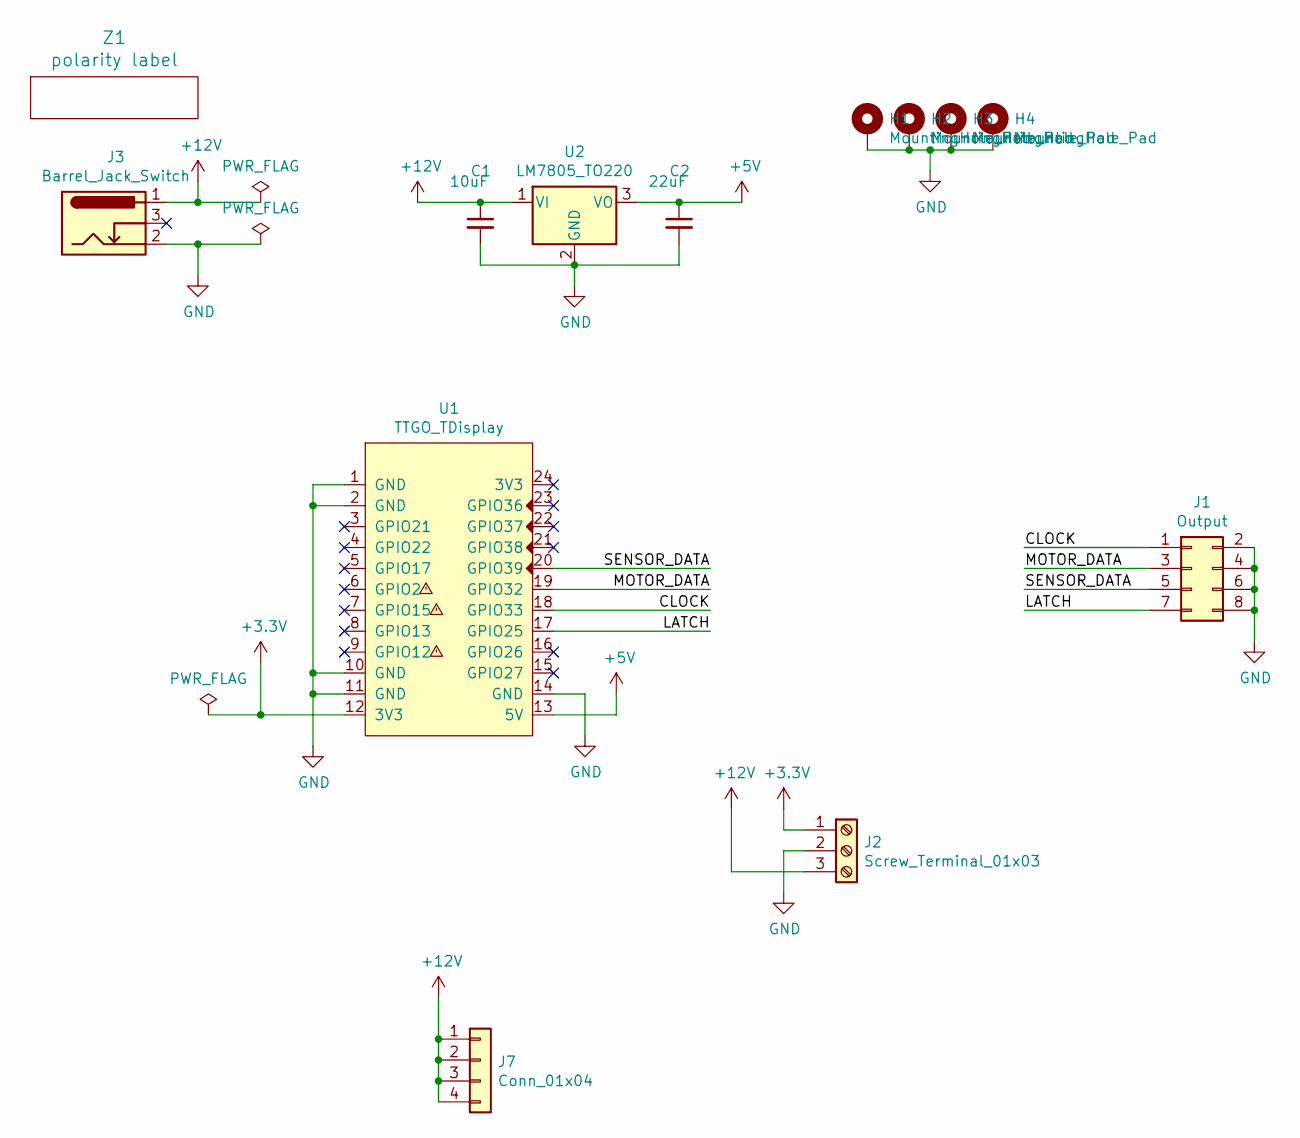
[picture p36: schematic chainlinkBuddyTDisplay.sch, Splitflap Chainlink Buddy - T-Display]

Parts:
C1: 10uF; C_1206_3216Metric_Pad1.33x1.80mm_HandSolder
C2: 22uF; C_1206_3216Metric_Pad1.33x1.80mm_HandSolder
H1, H2, H3, H4: MountingHole_Pad; MountingHole_3.2mm_M3_ISO7380_Pad
J1: Output; IDC-Header_2x04_P2.54mm_Vertical
J2: Screw_Terminal_01x03; Generic-5.08-3P
J3: Barrel_Jack_Switch; PJ-202A
J7: Conn_01x04; PinHoles_1x04_P2.54mm_NoSilk
U1: TTGO_TDisplay; T-DISPLAY_extra_pins_labeled_double
U2: LM7805_TO220; TO-220-3_Vertical
Z1: polarity label; Symbol_Barrel_Polarity

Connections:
+3V3: J2.1, U1.12 (3V3)
+5V: C2.1, U1.13 (5V), U2.3 (VO)
+12V: C1.1, J2.3, J3.1, J7.1, J7.2, J7.3, J7.4, U2.1 (VI)
/CLOCK: J1.1, U1.18 (GPIO33)
/LATCH: J1.7, U1.17 (GPIO25)
/MOTOR_DATA: J1.3, U1.19 (GPIO32)
/SENSOR_DATA: J1.5, U1.20 (GPIO39)
GND: C1.2, C2.2, H1.1, H2.1, H3.1, H4.1, J1.2, J1.4, J1.6, J1.8, J2.2, J3.2, U1.1 (GND), U1.2 (GND), U1.10 (GND), U1.11 (GND), U1.14 (GND), U2.2 (GND)

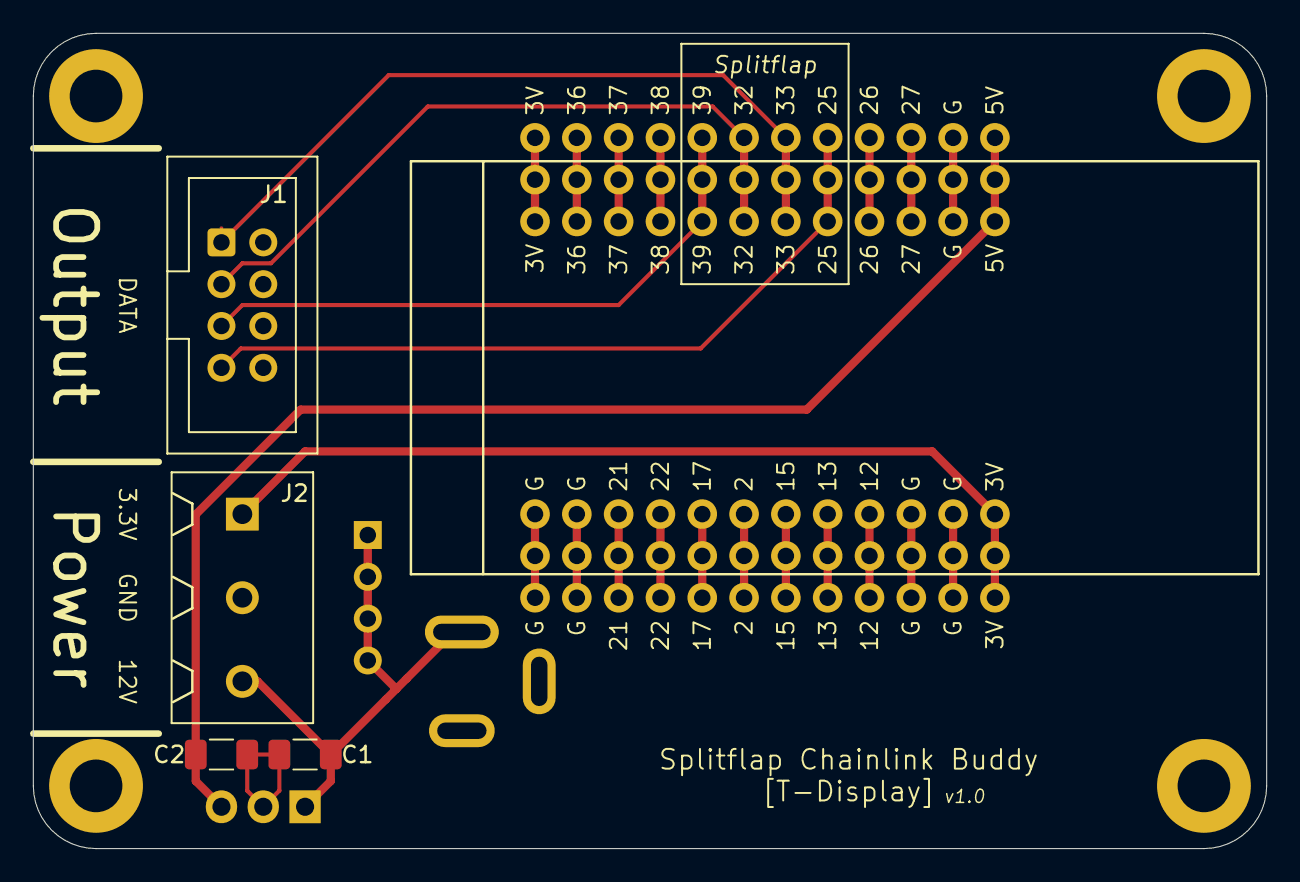
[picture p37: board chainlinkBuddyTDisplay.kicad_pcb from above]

Board: 2 copper layers, 74.9 x 49.5 mm, 13 parts (1 on the bottom side), 8 nets.

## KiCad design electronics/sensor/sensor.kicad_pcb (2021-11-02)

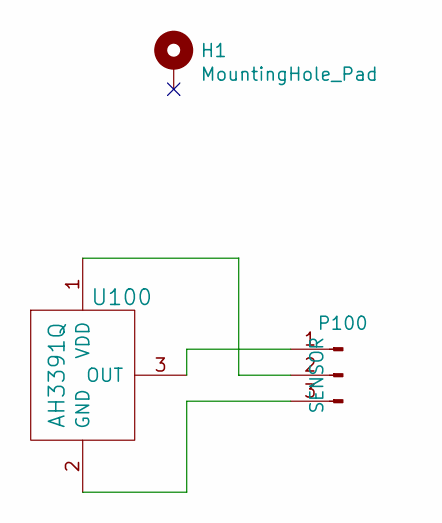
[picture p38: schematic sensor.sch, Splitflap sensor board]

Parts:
H1: MountingHole_Pad; M4_mount
P100: SENSOR; Pin_Header_Right_Angle_1x03
U100: AH3391Q; hall_effect_wide

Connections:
unnamed: P100.1, U100.3 (OUT)
unnamed: P100.2, U100.1 (VDD)
unnamed: P100.3, U100.2 (GND)

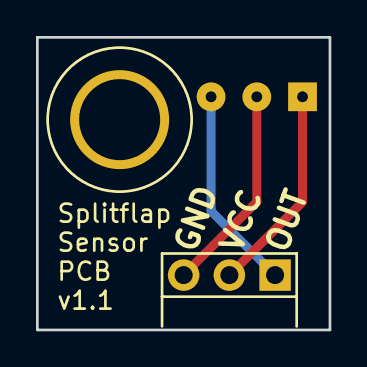
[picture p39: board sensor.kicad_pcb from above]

Board: 2 copper layers, 16.3 x 16.3 mm, 3 parts (1 on the bottom side), 3 nets.

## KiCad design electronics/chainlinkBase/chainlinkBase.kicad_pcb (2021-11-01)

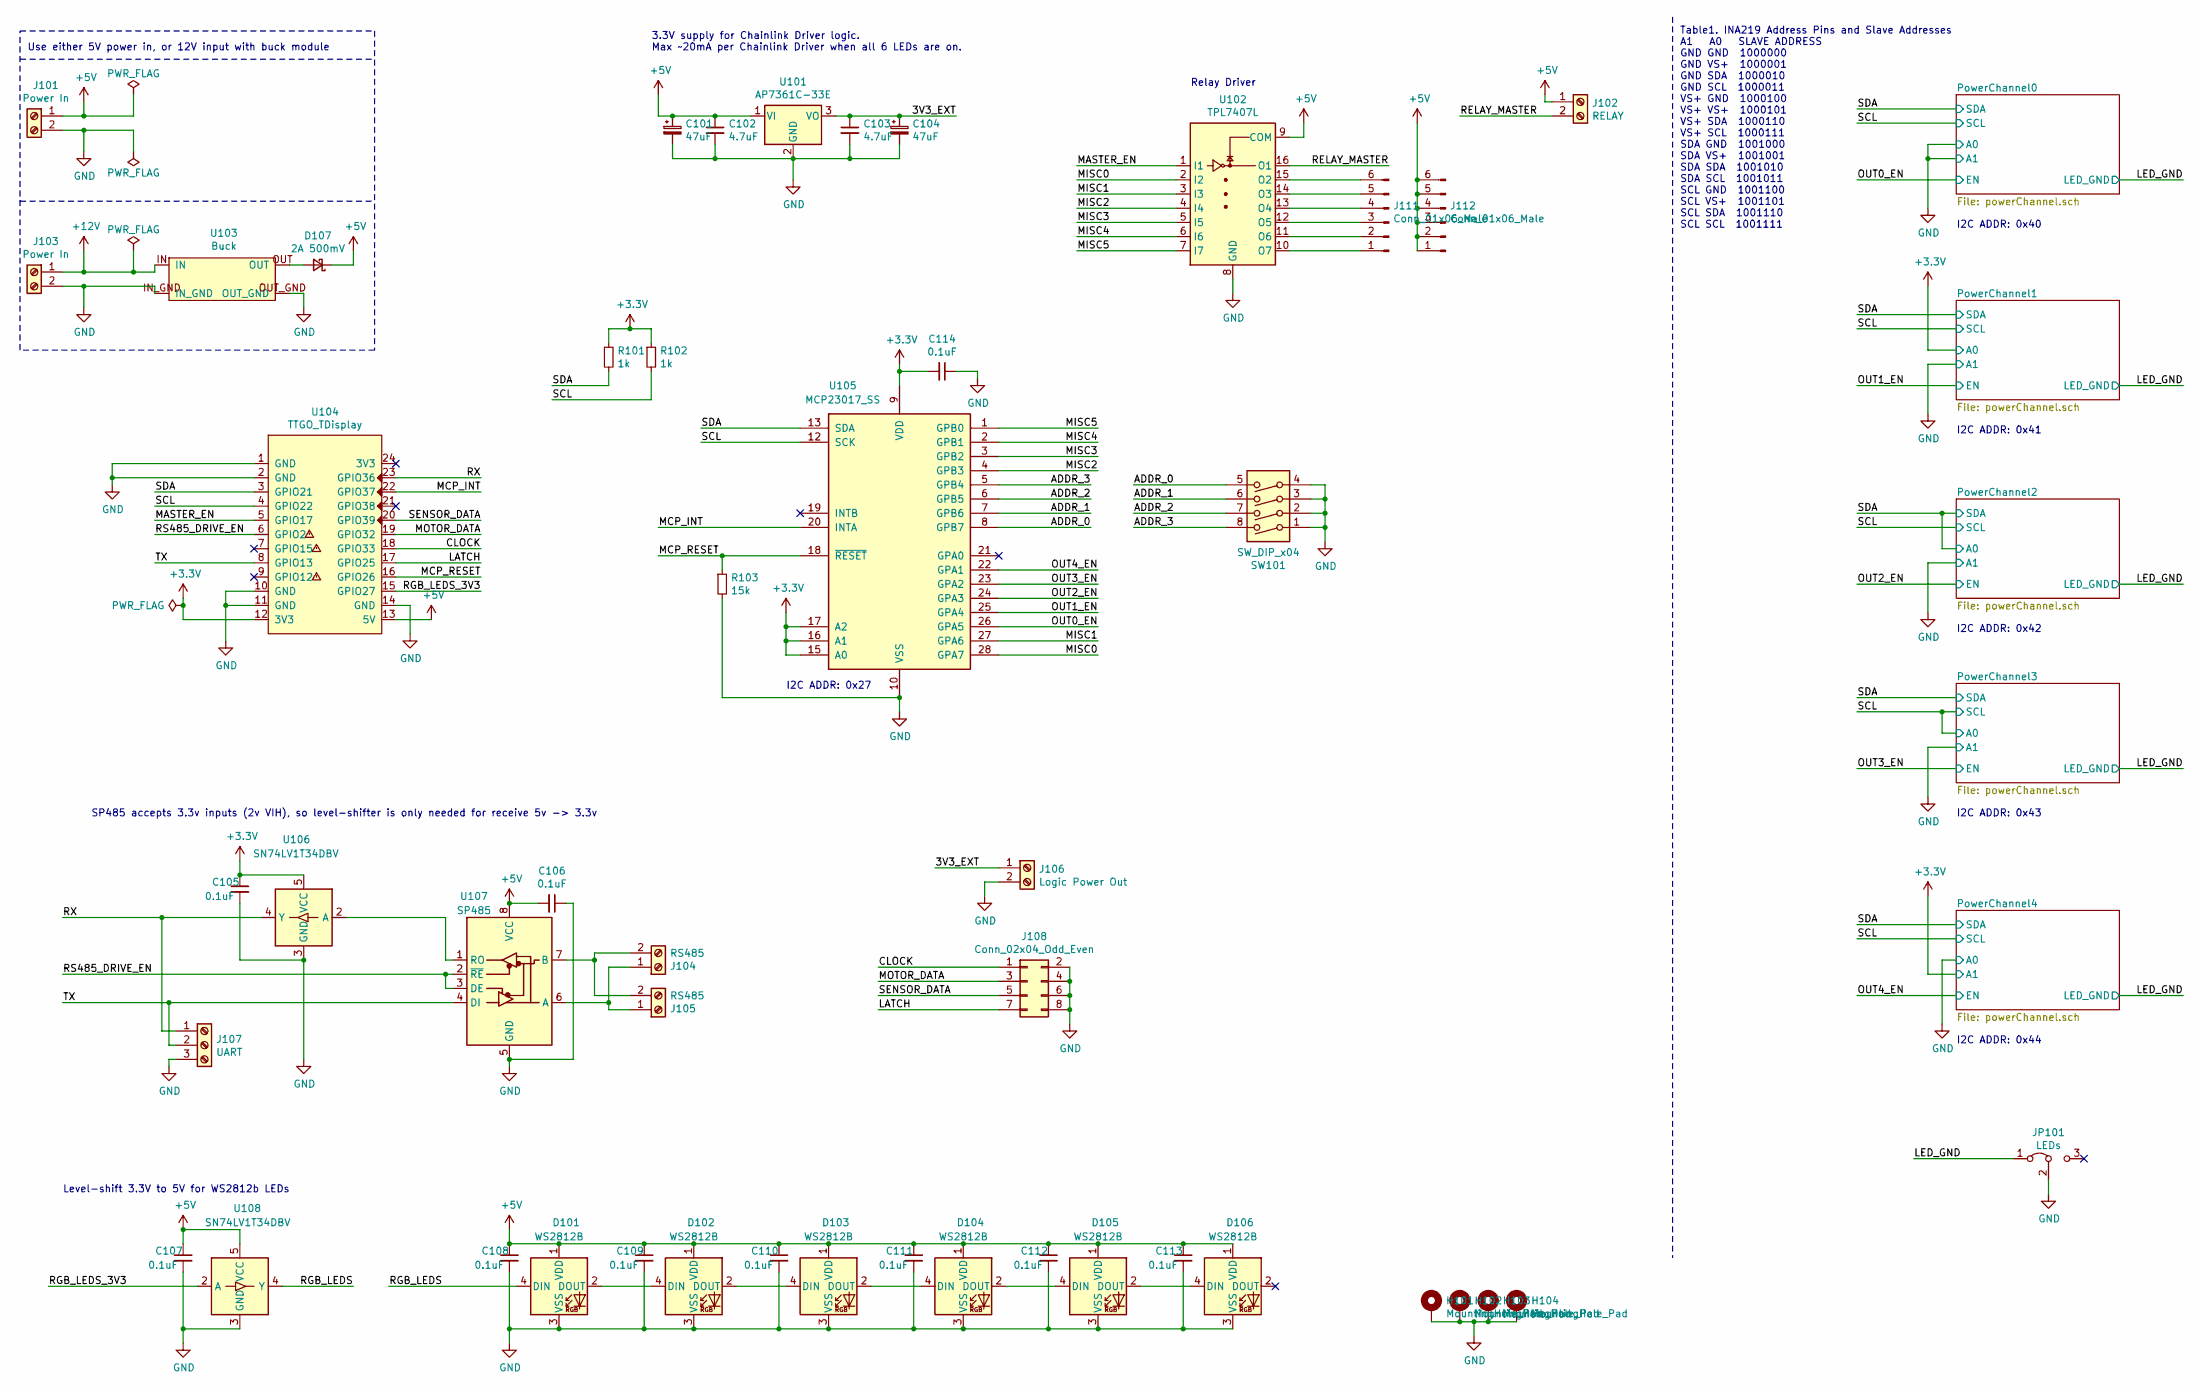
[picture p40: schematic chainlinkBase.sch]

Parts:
C101, C104: 47uF; CP_Elec_6.3x5.4
C102, C103: 4.7uF; C_0805_2012Metric
C105, C106, C107, C108, C109, C110, C111, C112, C113, C114: 0.1uF; C_0805_2012Metric
D101, D102, D103, D104, D105, D106: WS2812B; LED_WS2812B_PLCC4_5.0x5.0mm_P3.2mm
D107: 2A 500mV; D_SOD-128
H101, H102, H103, H104: MountingHole_Pad; MountingHole_3.2mm_M3_ISO7380_Pad
J101, J103: Power In; Generic-5.08-2P
J102: RELAY; Generic-5.08-2P
J104, J105: RS485; Generic-5.08-2P
J106: Logic Power Out; Generic-5.08-2P
J107: UART; Generic-5.08-3P
J108: Conn_02x04_Odd_Even; IDC-Header_2x04_P2.54mm_Vertical
J111, J112: Conn_01x06_Male; PinHeader_1x06_P2.54mm_Vertical
JP101: LEDs; PinHeader_1x03_P2.54mm_Vertical_SolderJumper
R101, R102: 1k; R_0805_2012Metric
R103: 15k; R_0805_2012Metric
SW101: SW_DIP_x04; SW_DIP_SPSTx04_Slide_Omron_A6S-410x_W8.9mm_P2.54mm
U101: AP7361C-33E; SOT-223-3_TabPin2
U102: TPL7407L; SOIC-16_3.9x9.9mm_P1.27mm_silk
U103: Buck; BuckModuleBackSilk
U104: TTGO_TDisplay; T-DISPLAY_extra_pins_labeled
U105: MCP23017_SS; SSOP-28_5.3x10.2mm_P0.65mm
U106, U108: SN74LV1T34DBV; SOT-23-5
U107: SP485; SOIC-8_3.9x4.9mm_P1.27mm

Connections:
+3V3: C105.1, C114.2, R101.1, R102.1, U104.12 (3V3), U105.9 (VDD), U105.15 (A0), U105.16 (A1), U105.17 (A2), U106.5 (VCC); also elsewhere on the board
+5V: C101.1, C102.1, C106.2, C107.1, C108.1, C109.1, C110.1, C111.1, C112.1, C113.1, D101.1 (VDD), D102.1 (VDD), D103.1 (VDD), D104.1 (VDD), D105.1 (VDD), D106.1 (VDD), D107.1 (K), J101.1, J102.1, J112.1, J112.2, J112.3, J112.4, J112.5, J112.6, U101.1 (VI), U102.9 (COM), U104.13 (5V), U107.8 (VCC), U108.5 (VCC)
+12V: J103.1, U103.IN
/3V3_EXT: C103.1, C104.1, J106.1, U101.3 (VO)
/ADDR_0: SW101.5, U105.8 (GPB7)
/ADDR_1: SW101.6, U105.7 (GPB6)
/ADDR_2: SW101.7, U105.6 (GPB5)
/ADDR_3: SW101.8, U105.5 (GPB4)
/CLOCK: J108.1, U104.18 (GPIO33)
/LATCH: J108.7, U104.17 (GPIO25)
/LED_GND: JP101.1 (A); also elsewhere on the board
/MASTER_EN: U102.1 (I1), U104.5 (GPIO17)
/MCP_INT: U104.22 (GPIO37), U105.20 (INTA)
/MCP_RESET: R103.1, U104.16 (GPIO26), U105.18 (~RESET~)
/MISC0: U102.2 (I2), U105.28 (GPA7)
/MISC1: U102.3 (I3), U105.27 (GPA6)
/MISC2: U102.4 (I4), U105.4 (GPB3)
/MISC3: U102.5 (I5), U105.3 (GPB2)
/MISC4: U102.6 (I6), U105.2 (GPB1)
/MISC5: U102.7 (I7), U105.1 (GPB0)
/MOTOR_DATA: J108.3, U104.19 (GPIO32)
/OUT0_EN: U105.26 (GPA5); also elsewhere on the board
/OUT1_EN: U105.25 (GPA4); also elsewhere on the board
/OUT2_EN: U105.24 (GPA3); also elsewhere on the board
/OUT3_EN: U105.23 (GPA2); also elsewhere on the board
/OUT4_EN: U105.22 (GPA1); also elsewhere on the board
/RELAY_MASTER: J102.2, U102.16 (O1)
/RGB_LEDS: D101.4 (DIN), U108.4 (Y)
/RGB_LEDS_3V3: U104.15 (GPIO27), U108.2 (A)
/RS485_DRIVE_EN: U104.6 (GPIO2), U107.2 (~RE), U107.3 (DE)
/RX: J107.1, U104.23 (GPIO36), U106.4 (Y)
/SCL: R102.2, U104.4 (GPIO22), U105.12 (SCK); also elsewhere on the board
/SDA: R101.2, U104.3 (GPIO21), U105.13 (SDA); also elsewhere on the board
/SENSOR_DATA: J108.5, U104.20 (GPIO39)
/TX: J107.2, U104.8 (GPIO13), U107.4 (DI)
GND: C101.2, C102.2, C103.2, C104.2, C105.2, C106.1, C107.2, C108.2, C109.2, C110.2, C111.2, C112.2, C113.2, C114.1, D101.3 (VSS), D102.3 (VSS), D103.3 (VSS), D104.3 (VSS), D105.3 (VSS), D106.3 (VSS), H101.1, H102.1, H103.1, H104.1, J101.2, J103.2, J106.2, J107.3, J108.2, J108.4, J108.6, J108.8, JP101.2 (C), R103.2, SW101.1, SW101.2, SW101.3, SW101.4, U101.2 (GND), U102.8 (GND), U103.IN_GND, U103.OUT_GND, U104.1 (GND), U104.2 (GND), U104.10 (GND), U104.11 (GND), U104.14 (GND), U105.10 (VSS), U106.3 (GND), U107.5 (GND), U108.3 (GND); also elsewhere on the board
unnamed: D101.2 (DOUT), D102.4 (DIN)
unnamed: D102.2 (DOUT), D103.4 (DIN)
unnamed: D103.2 (DOUT), D104.4 (DIN)
unnamed: D104.2 (DOUT), D105.4 (DIN)
unnamed: D105.2 (DOUT), D106.4 (DIN)
unnamed: D107.2 (A), U103.OUT
unnamed: J104.1, J105.1, U107.6 (A)
unnamed: J104.2, J105.2, U107.7 (B)
unnamed: J111.1, U102.10 (O7)
unnamed: J111.2, U102.11 (O6)
unnamed: J111.3, U102.12 (O5)
unnamed: J111.4, U102.13 (O4)
unnamed: J111.5, U102.14 (O3)
unnamed: J111.6, U102.15 (O2)
unnamed: U106.2 (A), U107.1 (RO)

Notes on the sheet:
Relay Driver
I2C ADDR: 0x27
I2C ADDR: 0x40
Level-shift 3.3V to 5V for WS2812b LEDs
SP485 accepts 3.3v inputs (2v VIH), so level-shifter is only needed for receive 5v -> 3.3v
3.3V supply for Chainlink Driver logic. Max ~~20mA per Chainlink Driver when all 6 LEDs are on.
Use either 5V power in, or 12V input with buck module
Table1. INA219 Address Pins and Slave Addresses A1 A0 SLAVE ADDRESS GND GND 1000000 GND VS+ 1000001 GND SDA 1000010 GND SCL 1000011 VS+ GND 1000100 VS+ VS+ 1000101 VS+ SDA 1000110 VS+ SCL 1000111 SDA GND 1001000 SDA VS+ 1001001 SDA SDA 1001010 SDA SCL 1001011 SCL GND 1001100 SCL VS+ 1001101 SCL SDA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
I2C ADDR: 0x41
I2C ADDR: 0x42
I2C ADDR: 0x43
I2C ADDR: 0x44

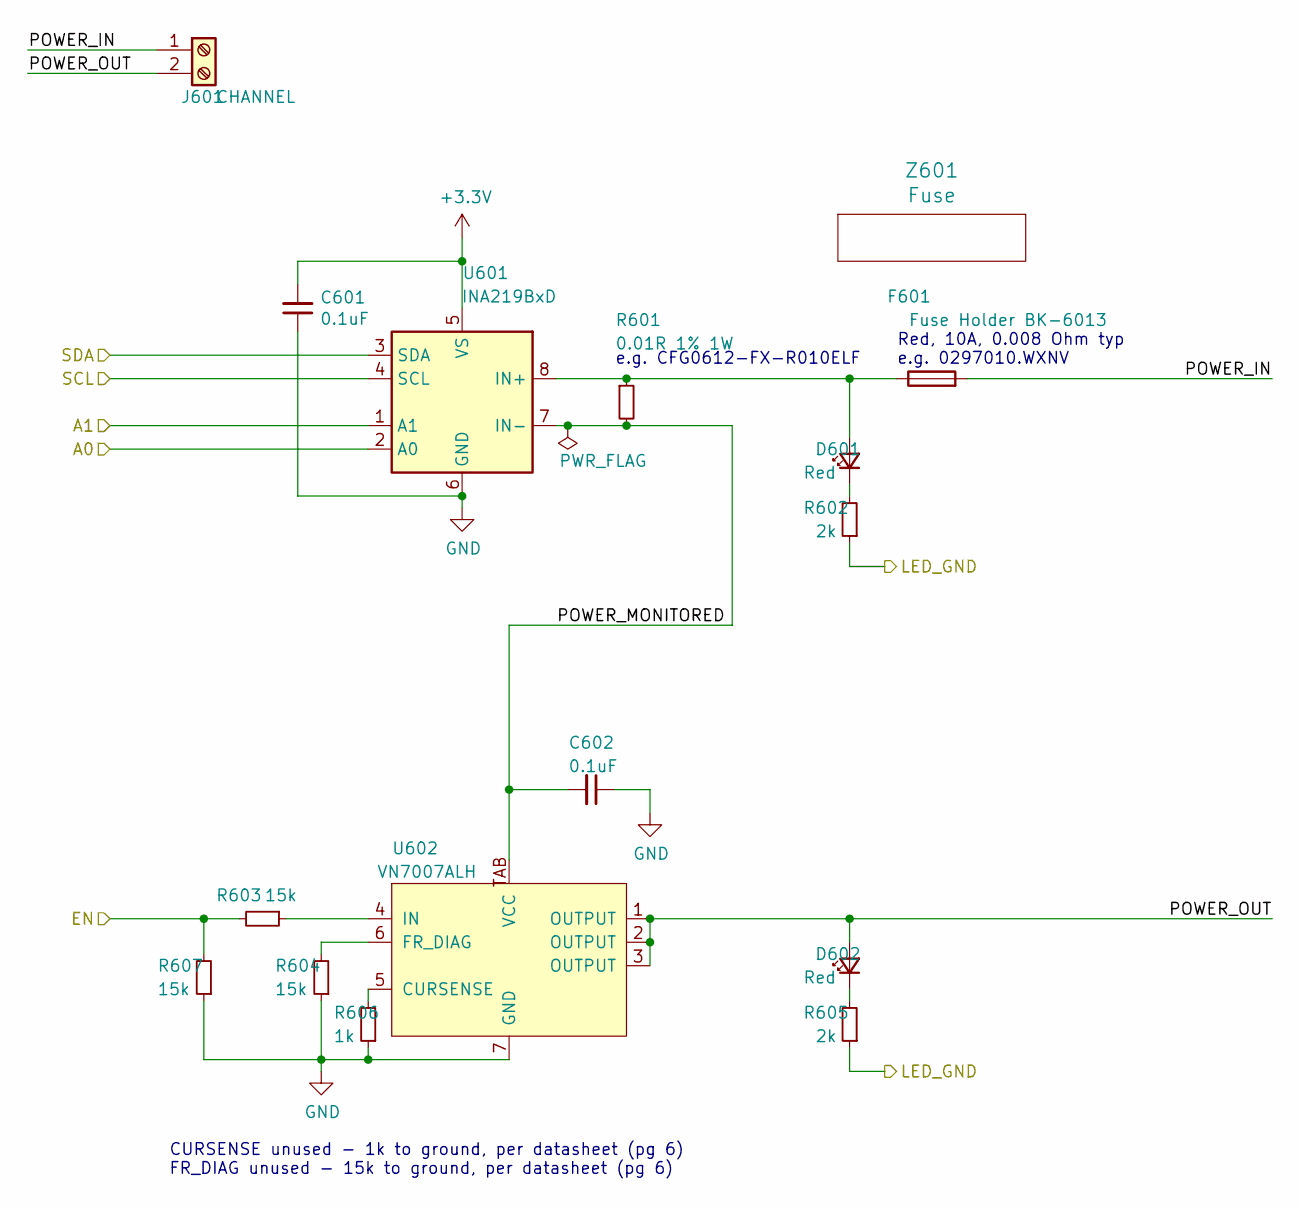
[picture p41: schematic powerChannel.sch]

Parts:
C201, C202: 0.1uF; C_0805_2012Metric
D201, D202: Red; LED_0805_2012Metric_Silkscreen
F201: Fuse Holder BK-6013; BK-6013
J201: CHANNEL; Generic-5.08-2P
R201: 0.01R 1% 1W; R_0612_1632Metric
R202, R205: 2k; R_0805_2012Metric
R203, R204, R207: 15k; R_0805_2012Metric
R206: 1k; R_0805_2012Metric
U201: INA219BxD; SOIC-8_3.9x4.9mm_P1.27mm
U202: VN7007ALH; VN7007ALHTR
Z201: Fuse; Dummy

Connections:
+3V3: C201.2, U201.5 (VS); also elsewhere on the board
/LED_GND: R202.1, R205.1; also elsewhere on the board
/OUT0_EN: R203.2, R207.2; also elsewhere on the board
/PowerChannel0/POWER_IN: F201.2, J201.1
/PowerChannel0/POWER_MONITORED: C202.2, R201.2, U201.7 (IN-), U202.TAB (VCC)
/PowerChannel0/POWER_OUT: D202.2 (A), J201.2, U202.1 (OUTPUT), U202.2 (OUTPUT), U202.3 (OUTPUT)
/SCL: U201.4 (SCL); also elsewhere on the board
/SDA: U201.3 (SDA); also elsewhere on the board
GND: C201.1, C202.1, R204.1, R206.1, R207.1, U201.1 (A1), U201.2 (A0), U201.6 (GND), U202.7 (GND); also elsewhere on the board
unnamed: D201.1 (K), R202.2
unnamed: D201.2 (A), F201.1, R201.1, U201.8 (IN+)
unnamed: D202.1 (K), R205.2
unnamed: R203.1, U202.4 (IN)
unnamed: R204.2, U202.6 (FR_DIAG)
unnamed: R206.2, U202.5 (CURSENSE)

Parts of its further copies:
C301, C302, C401, C402, C501, C502, C601, C602: 0.1uF; C_0805_2012Metric
D301, D302, D401, D402, D501, D502, D601, D602: Red; LED_0805_2012Metric_Silkscreen
F301, F401, F501, F601: Fuse Holder BK-6013; BK-6013
J301, J401, J501, J601: CHANNEL; Generic-5.08-2P
R301, R401, R501, R601: 0.01R 1% 1W; R_0612_1632Metric
R302, R305, R402, R405, R502, R505, R602, R605: 2k; R_0805_2012Metric
R303, R304, R307, R403, R404, R407, R503, R504, R507, R603, R604, R607: 15k; R_0805_2012Metric
R306, R406, R506, R606: 1k; R_0805_2012Metric
U301, U401, U501, U601: INA219BxD; SOIC-8_3.9x4.9mm_P1.27mm
U302, U402, U502, U602: VN7007ALH; VN7007ALHTR
Z301, Z401, Z501, Z601: Fuse; Dummy

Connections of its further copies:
+3V3: C301.2, C401.2, C501.2, C601.2, U301.2 (A0), U301.5 (VS), U401.5 (VS), U501.5 (VS), U601.1 (A1), U601.5 (VS); also elsewhere on the board
/LED_GND: R302.1, R305.1, R402.1, R405.1, R502.1, R505.1, R602.1, R605.1; also elsewhere on the board
/OUT1_EN: R303.2, R307.2; also elsewhere on the board
/OUT2_EN: R403.2, R407.2; also elsewhere on the board
/OUT3_EN: R503.2, R507.2; also elsewhere on the board
/OUT4_EN: R603.2, R607.2; also elsewhere on the board
/PowerChannel1/POWER_IN: F301.2, J301.1
/PowerChannel1/POWER_MONITORED: C302.2, R301.2, U301.7 (IN-), U302.TAB (VCC)
/PowerChannel1/POWER_OUT: D302.2 (A), J301.2, U302.1 (OUTPUT), U302.2 (OUTPUT), U302.3 (OUTPUT)
/PowerChannel2/POWER_IN: F401.2, J401.1
/PowerChannel2/POWER_MONITORED: C402.2, R401.2, U401.7 (IN-), U402.TAB (VCC)
/PowerChannel2/POWER_OUT: D402.2 (A), J401.2, U402.1 (OUTPUT), U402.2 (OUTPUT), U402.3 (OUTPUT)
/PowerChannel3/POWER_IN: F501.2, J501.1
/PowerChannel3/POWER_MONITORED: C502.2, R501.2, U501.7 (IN-), U502.TAB (VCC)
/PowerChannel3/POWER_OUT: D502.2 (A), J501.2, U502.1 (OUTPUT), U502.2 (OUTPUT), U502.3 (OUTPUT)
/PowerChannel4/POWER_IN: F601.2, J601.1
/PowerChannel4/POWER_MONITORED: C602.2, R601.2, U601.7 (IN-), U602.TAB (VCC)
/PowerChannel4/POWER_OUT: D602.2 (A), J601.2, U602.1 (OUTPUT), U602.2 (OUTPUT), U602.3 (OUTPUT)
/SCL: U301.4 (SCL), U401.4 (SCL), U501.2 (A0), U501.4 (SCL), U601.4 (SCL); also elsewhere on the board
/SDA: U301.3 (SDA), U401.2 (A0), U401.3 (SDA), U501.3 (SDA), U601.3 (SDA); also elsewhere on the board
GND: C301.1, C302.1, C401.1, C402.1, C501.1, C502.1, C601.1, C602.1, R304.1, R306.1, R307.1, R404.1, R406.1, R407.1, R504.1, R506.1, R507.1, R604.1, R606.1, R607.1, U301.1 (A1), U301.6 (GND), U302.7 (GND), U401.1 (A1), U401.6 (GND), U402.7 (GND), U501.1 (A1), U501.6 (GND), U502.7 (GND), U601.2 (A0), U601.6 (GND), U602.7 (GND); also elsewhere on the board
unnamed: D301.1 (K), R302.2
unnamed: D301.2 (A), F301.1, R301.1, U301.8 (IN+)
unnamed: D302.1 (K), R305.2
unnamed: D401.1 (K), R402.2
unnamed: D401.2 (A), F401.1, R401.1, U401.8 (IN+)
unnamed: D402.1 (K), R405.2
unnamed: D501.1 (K), R502.2
unnamed: D501.2 (A), F501.1, R501.1, U501.8 (IN+)
unnamed: D502.1 (K), R505.2
unnamed: D601.1 (K), R602.2
unnamed: D601.2 (A), F601.1, R601.1, U601.8 (IN+)
unnamed: D602.1 (K), R605.2
unnamed: R303.1, U302.4 (IN)
unnamed: R304.2, U302.6 (FR_DIAG)
unnamed: R306.2, U302.5 (CURSENSE)
unnamed: R403.1, U402.4 (IN)
unnamed: R404.2, U402.6 (FR_DIAG)
unnamed: R406.2, U402.5 (CURSENSE)
unnamed: R503.1, U502.4 (IN)
unnamed: R504.2, U502.6 (FR_DIAG)
unnamed: R506.2, U502.5 (CURSENSE)
unnamed: R603.1, U602.4 (IN)
unnamed: R604.2, U602.6 (FR_DIAG)
unnamed: R606.2, U602.5 (CURSENSE)

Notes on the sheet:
e.g. CFG0612-FX-R010ELF
Red, 10A, 0.008 Ohm typ e.g. 0297010.WXNV
CURSENSE unused - 1k to ground, per datasheet (pg 6) FR_DIAG unused - 15k to ground, per datasheet (pg 6)

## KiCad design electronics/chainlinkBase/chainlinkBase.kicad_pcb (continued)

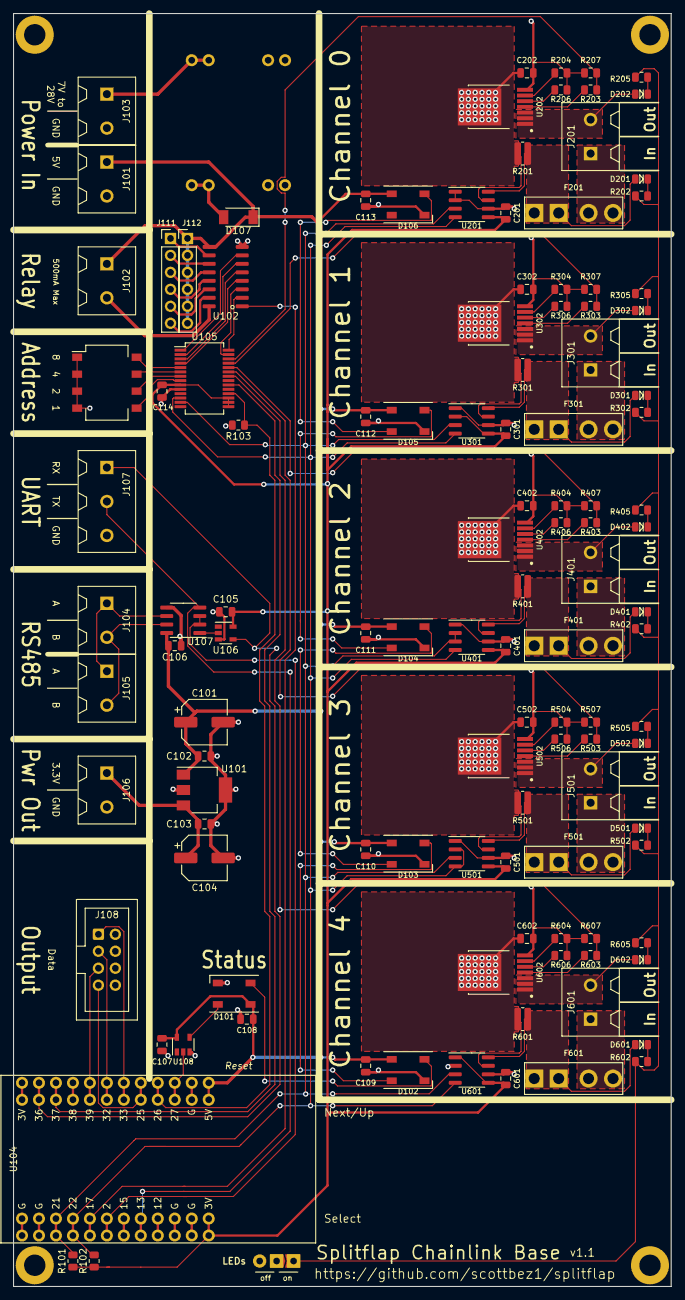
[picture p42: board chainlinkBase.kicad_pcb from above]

Board: 2 copper layers, 98.4 x 190.5 mm, 128 parts (0 on the bottom side), 96 nets.

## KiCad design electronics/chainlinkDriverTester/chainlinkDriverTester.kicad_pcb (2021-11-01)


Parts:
BZ1: Buzzer; Buzzer_12x9.5RM7.6
C1, C5: 10uF; CP_Elec_4x5.3; LCSC C134721
C2, C4: 4.7uF; C_0805_2012Metric
C3: 10uF; C_1206_3216Metric
C6, C7: 0.1uF; C_0805_2012Metric
C8: 22uF; C_1206_3216Metric
D1, D2, D4: Red; LED_0805_2012Metric_Silkscreen
D3, D7: 2A 500mV; D_SOD-128
F1: 50mA (0ZCM0005FF2G); Fuse_0603_1608Metric
F2: Fuse Holder BK-6013; BK-6013
H1, H2, H3, H4, H5, H6, H7, H8, H9, H10, H11, H12, H13, H14, H15, H16: MountingHole; MountingHole_3.2mm_M3_ISO7380_Pad
J1: Barrel_Jack_Switch; PJ-202A
J2: Conn_01x03_Female; PinSocket_1x03_P2.54mm_Vertical
J3: Motor A; JST_XH_B5B-XH-A_1x05_P2.50mm_Vertical
J5: Motor B; JST_XH_B5B-XH-A_1x05_P2.50mm_Vertical
J6: Motor C; JST_XH_B5B-XH-A_1x05_P2.50mm_Vertical
J7: Motor D; JST_XH_B5B-XH-A_1x05_P2.50mm_Vertical
J8: Sensor A; PinHeader_1x03_P2.54mm_Vertical
J9: Sensor B; PinHeader_1x03_P2.54mm_Vertical
J10: Sensor C; PinHeader_1x03_P2.54mm_Vertical
J11: Sensor D; PinHeader_1x03_P2.54mm_Vertical
J12: Motor E; JST_XH_B5B-XH-A_1x05_P2.50mm_Vertical
J13: Motor F; JST_XH_B5B-XH-A_1x05_P2.50mm_Vertical
J14: Sensor E; PinHeader_1x03_P2.54mm_Vertical
J15: Sensor F; PinHeader_1x03_P2.54mm_Vertical
J22: Power; Generic-5.08-2P; LCSC C8465
J26, J27, J28, J29, J30, J31: exp; PinHeader_1x04_P2.54mm_Vertical
J101: Conn_02x04_Odd_Even; IDC-Header_2x04_P2.54mm_Vertical
R1, R2, R8: 1k; R_0805_2012Metric
R3, R4, R5, R6, R10: 15k; R_0805_2012Metric
R7, R11, R13: 220; R_0805_2012Metric
R9: 2k; R_0805_2012Metric
R12: 0.01R 1% 1W; R_0612_1632Metric
SW1: SW_Push; ESE13V01D
TP1, TP2, TP3, TP4, TP5, TP6, TP7, TP8, TP9, TP10, TP11, TP12, TP13, TP14, TP15, TP16, TP17, TP18, TP19, TP20, TP21, TP22, TP23, TP24, TP25, TP26, TP27, TP28, TP29, TP30, TP31, TP32, TP33, TP34, TP35, TP36, TP37, TP38, TP39, TP40, TP41, TP42, TP43, TP44, TP45, TP46, TP47, TP48, TP49, TP50, TP51, TP52, TP53, TP54, TP55, TP56, TP59, TP60, TP63, TP64, TP65, TP66, TP67, TP68: TestPoint; pogo1mm
TP74: TestPoint; TestPoint_THTPad_D2.0mm_Drill1.0mm
U1: AP7361C-33E; SOT-223-3_TabPin2
U2: TTGO_TDisplay; T-DISPLAY_extra_pins
U3: VN7007ALH; VN7007ALHTR
U4: MCP23017_SS; SSOP-28_5.3x10.2mm_P0.65mm
U5: INA219BxD; SOIC-8_3.9x4.9mm_P1.27mm
U6: LM7805_TO220; TO-220-3_Vertical
U7: Buck; BuckModuleBackSilk
Z101: Fuse; Dummy

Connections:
+5V: C1.1, C2.2, D7.1 (K), U1.1 (VI), U2.13 (5V)
+12V: F2.2, J1.1, J22.1
/3V3_FUSED: D4.2 (A), F1.1, J2.1, TP63.1, TP64.1, U2.23 (GPIO36)
/12V_EN: D1.2 (A), R3.2, R5.2, U2.8 (GPIO13)
/12V_OUTPUT: J2.3, R12.2, TP67.1, TP68.1, U5.7 (IN-)
/12V_TEST_FEED: R11.1, U2.15 (GPIO27)
/BUZZER: BZ1.1 (-), U4.4 (GPB3)
/CLOCK: TP49.1, U2.18 (GPIO33)
/CLOCK_OUT: J101.1, TP50.1
/DETECT: SW1.1, U4.5 (GPB4)
/GPA0: J26.1, U4.21 (GPA0)
/GPA1: J26.2, U4.22 (GPA1)
/GPA2: J26.3, U4.23 (GPA2)
/GPA3: J26.4, U4.24 (GPA3)
/GPA4: J29.1, U4.25 (GPA4)
/GPA5: J29.2, U4.26 (GPA5)
/GPA6: J29.3, U4.27 (GPA6)
/GPA7: J29.4, U4.28 (GPA7)
/LATCH: TP55.1, U2.17 (GPIO25)
/LATCH_OUT: J101.7, TP56.1
/MCP_INT: R4.1, U2.22 (GPIO37), U4.20 (INTA)
/MCP_RESET: R10.1, U2.16 (GPIO26), U4.18 (~RESET~)
/MOTOR_DATA: TP51.1, U2.19 (GPIO32)
/MOTOR_OUT: J101.3, TP52.1
/OUT_A_COMMON: J3.5, TP37.1
/OUT_A_PHASE_A: J3.1, TP10.1
/OUT_A_PHASE_B: J3.2, TP16.1
/OUT_A_PHASE_C: J3.3, TP23.1
/OUT_A_PHASE_D: J3.4, TP30.1
/OUT_B_COMMON: J5.5, TP38.1
/OUT_B_PHASE_A: J5.1, TP11.1
/OUT_B_PHASE_B: J5.2, TP17.1
/OUT_B_PHASE_C: J5.3, TP24.1
/OUT_B_PHASE_D: J5.4, TP31.1
/OUT_C_COMMON: J6.5, TP39.1
/OUT_C_PHASE_A: J6.1, TP12.1
/OUT_C_PHASE_B: J6.2, TP18.1
/OUT_C_PHASE_C: J6.3, TP25.1
/OUT_C_PHASE_D: J6.4, TP32.1
/OUT_D_COMMON: J7.5, TP40.1
/OUT_D_PHASE_A: J7.1, TP13.1
/OUT_D_PHASE_B: J7.2, TP19.1
/OUT_D_PHASE_C: J7.3, TP26.1
/OUT_D_PHASE_D: J7.4, TP33.1
/OUT_E_COMMON: J12.5, TP41.1
/OUT_E_PHASE_A: J12.1, TP14.1
/OUT_E_PHASE_B: J12.2, TP20.1
/OUT_E_PHASE_C: J12.3, TP27.1
/OUT_E_PHASE_D: J12.4, TP34.1
/OUT_F_COMMON: J13.5, TP42.1
/OUT_F_PHASE_A: J13.1, TP15.1
/OUT_F_PHASE_B: J13.2, TP21.1
/OUT_F_PHASE_C: J13.3, TP28.1
/OUT_F_PHASE_D: J13.4, TP35.1
/SCL: R2.2, U2.4 (GPIO22), U4.12 (SCK), U5.4 (SCL)
/SDA: R1.2, U2.3 (GPIO21), U4.13 (SDA), U5.3 (SDA)
/SENSOR_A_GND: J8.1, TP3.1
/SENSOR_A_SIGNAL: J8.3, TP1.1, U4.1 (GPB0)
/SENSOR_A_VCC: J8.2, TP2.1
/SENSOR_B_GND: J9.1, TP6.1
/SENSOR_B_SIGNAL: J9.3, TP4.1, U4.2 (GPB1)
/SENSOR_B_VCC: J9.2, TP5.1
/SENSOR_C_GND: J10.1, TP9.1
/SENSOR_C_SIGNAL: J10.3, TP7.1, U4.3 (GPB2)
/SENSOR_C_VCC: J10.2, TP8.1
/SENSOR_DATA: TP53.1, U2.20 (GPIO39)
/SENSOR_D_GND: J11.1, TP36.1
/SENSOR_D_SIGNAL: J11.3, TP22.1, U4.6 (GPB5)
/SENSOR_D_VCC: J11.2, TP29.1
/SENSOR_E_GND: J14.1, TP45.1
/SENSOR_E_SIGNAL: J14.3, TP43.1, U4.7 (GPB6)
/SENSOR_E_VCC: J14.2, TP44.1
/SENSOR_F_GND: J15.1, TP48.1
/SENSOR_F_SIGNAL: J15.3, TP46.1, U4.8 (GPB7)
/SENSOR_F_VCC: J15.2, TP47.1
/SENSOR_IN: J101.5, TP54.1
/SW_IN: C3.1, F2.1, U3.TAB (VCC), U6.1 (VI), U7.IN
GND: BZ1.2 (+), C1.2, C2.1, C3.2, C4.1, C5.2, C6.2, C7.1, C8.2, J1.2, J1.3, J2.2, J22.2, J28.1, J28.2, J28.3, J28.4, J31.1, J31.2, J31.3, J31.4, J101.2, J101.4, J101.6, J101.8, R5.1, R6.1, R7.1, R8.1, R9.1, R10.2, R13.1, SW1.2, TP59.1, TP60.1, TP65.1, TP66.1, U1.2 (GND), U2.1 (GND), U2.2 (GND), U2.10 (GND), U2.11 (GND), U2.14 (GND), U3.7 (GND), U4.10 (VSS), U4.15 (A0), U4.16 (A1), U4.17 (A2), U5.1 (A1), U5.2 (A0), U5.6 (GND), U6.2 (GND), U7.IN_GND, U7.OUT_GND
unnamed: C4.2, C5.1, F1.2, TP74.1, U1.3 (VO)
unnamed: C8.1, D7.2 (A), U6.3 (VO), U7.OUT
unnamed: D1.1 (K), R7.2
unnamed: D2.1 (K), R9.2
unnamed: D2.2 (A), D3.1 (K), R12.1, U3.1 (OUTPUT), U3.2 (OUTPUT), U3.3 (OUTPUT), U5.8 (IN+)
unnamed: D3.2 (A), R11.2
unnamed: D4.1 (K), R13.2
unnamed: R3.1, U3.4 (IN)
unnamed: R6.2, U3.6 (FR_DIAG)
unnamed: R8.2, U3.5 (CURSENSE)

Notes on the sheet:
Violet, 3A, 0.03375 Ohm typ e.g. 0297003.WXNV
I2C ADDR: 0x40
e.g. CFG0612-FX-R010ELF
I2C ADDR: 0x20

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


Board: 2 copper layers, 198.1 x 95.2 mm, 141 parts (12 on the bottom side), 89 nets.

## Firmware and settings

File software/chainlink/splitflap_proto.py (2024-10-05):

import argparse
from cobs import cobs
from collections import (
    defaultdict,
)
from contextlib import contextmanager
from enum import Enum
import logging
import os
from queue import (
    Empty,
    Full,
    Queue,
)
from random import randint
import serial
import serial.tools.list_ports
import six
import sys
from threading import (
    Thread,
    Lock,
)
import time
import zlib

software_root = os.path.dirname(os.path.abspath(__file__))
sys.path.append(os.path.join(software_root, 'proto_gen'))

from proto_gen import splitflap_pb2

SPLITFLAP_BAUD = 230400


class Splitflap(object):

    class ForceMovement(Enum):
        NONE = 1            # No movement if module is already at the specified character
        ONLY_NON_BLANK = 2  # Force a full revolution if module is already at the specified character, but only if it's not the blank (' ') character
        ALL = 3             # All modules move on every command, regardless of whether they are already at the specified character

    RETRY_TIMEOUT = 0.25

    _LEGACY_ALPHABET = [
        ' ', 'A', 'B', 'C', 'D', 'E', 'F', 'G', 'H', 'I',
        'J', 'K', 'L', 'M', 'N', 'O', 'P', 'Q', 'R', 'S',
        'T', 'U', 'V', 'W', 'X', 'Y', 'Z', '0', '1', '2',
        '3', '4', '5', '6', '7', '8', '9', '.', ',', "'",
    ]

    def __init__(self, serial_instance):
        self._serial = serial_instance
        self._logger = logging.getLogger('splitflap')
        self._out_q = Queue()
        self._ack_q = Queue()
        self._next_nonce = randint(0, 255)
        self._run = True

        self._lock = Lock()
        self._message_handlers = defaultdict(list)

        self._current_config = splitflap_pb2.SplitflapConfig()
        self._num_modules = None

        self._alphabet = Splitflap._LEGACY_ALPHABET
        self._alphabet_received = False

    def _read_loop(self):
        self._logger.debug('Read loop started')
        buffer = b''
        while True:
            buffer += self._serial.read_until(b'\0')
            if not self._run:
                return

            if not len(buffer):
                continue

            if not buffer.endswith(b'\0'):
                continue
            
            self._process_frame(buffer[:-1])
            buffer = b''

    def _process_frame(self, frame):
        try:
            decoded = cobs.decode(frame)
        except cobs.DecodeError:
            self._logger.debug(f'Failed decode ({len(frame)} bytes)')
            self._logger.debug(frame)
            return

        if len(decoded) < 4:
            return

        payload = decoded[:-4]
        expected_crc = zlib.crc32(payload) & 0xffffffff
        provided_crc = (decoded[-1] << 24) \
                        | (decoded[-2] << 16) \
                        | (decoded[-3] << 8) \
                        | decoded[-4]
        
        if expected_crc != provided_crc:
            self._logger.debug(f'Bad CRC. expected={hex(expected_crc)}, actual={hex(provided_crc)}')
            return

        message = splitflap_pb2.FromSplitflap()
        message.ParseFromString(payload)
        self._logger.debug(message)

        payload_type = message.WhichOneof('payload')

        # If this is an ack, notify the write thread
        if payload_type == 'ack':
            nonce = message.ack.nonce
            self._ack_q.put(nonce)
        elif payload_type == 'splitflap_state':
            num_modules_reported = len(message.splitflap_state.modules)
            if self._num_modules is None:
                self._num_modules = num_modules_reported
                for i in range(num_modules_reported):
                    self._current_config.modules.append(splitflap_pb2.SplitflapConfig.ModuleConfig())
            else:
                assert self._num_modules == num_modules_reported, f'Number of reported modules changed (was {self._num_modules}, now {num_modules_reported})'
        elif payload_type == 'general_state' and not self._alphabet_received:
            self._alphabet_received = True
            self._alphabet = list(message.general_state.flap_character_set.decode('utf-8'))

        with self._lock:
            for handler in self._message_handlers[payload_type] + self._message_handlers[None]:
                try:
                    handler(getattr(message, payload_type))
                except:
                    self._logger.warning(f'Unhandled exception in message handler ({payload_type})', exc_info=True)
    
    def _write_loop(self):
        self._logger.debug('Write loop started')
        while True:
            data = self._out_q.get()
            # Check for shutdown
            if not self._run:
                self._logger.debug('Write loop exiting @ _out_q')
                return
            (nonce, encoded_message) = data

            next_retry = 0
            while True:
                if time.time() >= next_retry:
                    if next_retry > 0:
                        self._logger.debug('Retry write...')
                    self._serial.write(encoded_message)
                    self._serial.write(b'\0')
                    next_retry = time.time() + Splitflap.RETRY_TIMEOUT
                
                try:
                    latest_ack_nonce = self._ack_q.get(timeout=next_retry - time.time())
                except Empty:
                    latest_ack_nonce = None

                # Check for shutdown
                if not self._run:
                    self._logger.debug('Write loop exiting @ _ack_q')
                    return

                if latest_ack_nonce == nonce:
                    break
                else:
                    self._logger.debug(f'Got unexpected nonce: {latest_ack_nonce}')
    
    def _enqueue_message(self, message):
        nonce = self._next_nonce
        self._next_nonce += 1

        message.nonce = nonce

        payload = bytearray(message.SerializeToString())

        crc = zlib.crc32(payload) & 0xffffffff
        payload.append(crc & 0xff)
        payload.append((crc >> 8) & 0xff)
        payload.append((crc >> 16) & 0xff)
        payload.append((crc >> 24) & 0xff)

        encoded_message = cobs.encode(payload)

        self._out_q.put((nonce, encoded_message))

        approx_q_length = self._out_q.qsize()
        self._logger.debug(f'Out q length: {approx_q_length}')
        if approx_q_length > 10:
            self._logger.warning(f'Output queue length is high! ({approx_q_length}) Is the splitflap still connected and functional?')

    def get_alphabet(self):
        return self._alphabet

    def set_text(self, text, force_movement=ForceMovement.NONE):
        """Helper for setting a string message. Using set_positions is preferable for more control."""

        # Transform text to a list of flap indexes (and pad with blanks so that all modules get updated even if text is shorter)
        positions = [self._alphabet.index(c) if c in self._alphabet else 0 for c in text] + [self._alphabet.index(' ')] * (self._num_modules - len(text))

        if force_movement == Splitflap.ForceMovement.NONE:
            force_movement = None
        elif force_movement == Splitflap.ForceMovement.ONLY_NON_BLANK:
            force_movement = [c in self._alphabet and c != ' ' for c in text] + [False] * (self._num_modules - len(text))
        elif force_movement == Splitflap.ForceMovement.ALL:
            force_movement = [True] * self._num_modules
        else:
            raise RuntimeError(f'bad value {force_movement}')

        self.set_positions(positions, force_movement)

    def set_positions(self, positions, force_movement=None):
        assert self._num_modules is not None, 'Cannot set positions before number of modules is known'

        assert len(positions) <= self._num_modules, 'More positions specified than modules'
        if force_movement is not None:
            assert len(positions) == len(force_movement), 'positions and force_movement list length must match'

        for i in range(len(positions)):
            if positions[i] is not None:
                self._current_config.modules[i].target_flap_index = positions[i]
            if force_movement is not None and force_movement[i]:
                self._current_config.modules[i].movement_nonce = (self._current_config.modules[i].movement_nonce + 1) % 256

        message = splitflap_pb2.ToSplitflap()
        message.splitflap_config.CopyFrom(self._current_config)
        self._enqueue_message(message)

    def start(self):
        self.read_thread = Thread(target=self._read_loop)
        self.write_thread = Thread(target=self._write_loop)
        self.read_thread.start()
        self.write_thread.start()
    
    def shutdown(self):
        self._logger.info('Shutting down...')
        self._run = False
        self.read_thread.join()
        self._logger.debug('Read thread terminated')
        self._out_q.put(None)
        self._ack_q.put(None)
        self.write_thread.join()
        self._logger.debug('Write thread terminated')
    
    def add_handler(self, message_type, handler):
        with self._lock:
            self._message_handlers[message_type].append(handler)
        return lambda: self._remove_handler(message_type, handler)

    def _remove_handler(self, message_type, handler):
        with self._lock:
            self._message_handlers[message_type].remove(handler)

    def request_state(self):
        message = splitflap_pb2.ToSplitflap()
        message.request_state.SetInParent()
        self._enqueue_message(message)

    def hard_reset(self):
        self._serial.setRTS(True)
        self._serial.setDTR(False)
        time.sleep(0.2)
        self._serial.setDTR(True)
        time.sleep(0.2)

    def get_num_modules(self):
        assert self._num_modules is not None, 'Num modules is unknown. Make sure to wait for a state message before querying'
        return self._num_modules


@contextmanager
def splitflap_context(serial_port, default_logging=True, wait_for_comms=True):
    with serial.Serial(serial_port, SPLITFLAP_BAUD, timeout=1.0) as ser:
        s = Splitflap(ser)
        s.start()

        if default_logging:
            s.add_handler('log', lambda msg: logging.info(f'From splitflap: {msg.msg}'))

        if wait_for_comms:
            logging.info('Connecting to splitflap...')
            q = Queue(1)
            def startup_handler(message):
                try:
                    q.put_nowait(None)
                except Full:
                    pass
            unregister = s.add_handler('splitflap_state', startup_handler)

            s.request_state()
            q.get()
            unregister()
            logging.info('Connected!')

        try:
            yield s
        finally:
            s.shutdown()


def ask_for_serial_port():
    print('Available ports:')
    ports = sorted(
        filter(
            lambda p: p.description != 'n/a',
            serial.tools.list_ports.comports(),
        ),
        key=lambda p: p.device,
    )
    for i, port in enumerate(ports):
        print('[{: 2}] {} - {}'.format(i, port.device, port.description))
    print()
    value = six.moves.input('Use which port? ')
    port_index = int(value)
    assert 0 <= port_index < len(ports)
    return ports[port_index].device


def _run_example():
    p = ask_for_serial_port()
    with splitflap_context(p) as s:
        modules = s.get_num_modules()
        alphabet = s.get_alphabet()

        # Set up a handler to log reported state changes
        def state_str(s):
            if s == splitflap_pb2.SplitflapState.ModuleState.State.NORMAL:
                return '\u2713'
            elif s == splitflap_pb2.SplitflapState.ModuleState.State.LOOK_FOR_HOME:
                return '\u2370'
            elif s == splitflap_pb2.SplitflapState.ModuleState.State.SENSOR_ERROR:
                return '\u26a0'
            elif s == splitflap_pb2.SplitflapState.ModuleState.State.PANIC:
                return '\u2342'
            elif s == splitflap_pb2.SplitflapState.ModuleState.State.DISABLED:
                return '\u29bb'


        last_state_string = ''
        def log_state(message):
            nonlocal last_state_string
            state_string = ''.join([alphabet[m.flap_index] if m.state == splitflap_pb2.SplitflapState.ModuleState.State.NORMAL else state_str(m.state) for m in message.modules])
            if state_string != last_state_string:
                logging.info('State: ' + state_string)
                last_state_string = state_string
        s.add_handler('splitflap_state', log_state)
        s.request_state()

        # Loop forever
        while True:
            text = input()[:modules]

            s.set_text(text, Splitflap.ForceMovement.ALL)


if __name__ == '__main__':
    parser = argparse.ArgumentParser('Splitflap python interface example')
    parser.add_argument('--verbose', '-v', action='store_true', help='Enable verbose logging')
    args = parser.parse_args()

    log_level = logging.DEBUG if args.verbose else logging.INFO
    logging.basicConfig(level=log_level, format='%(asctime)s:%(name)s:%(levelname)s:%(message)s')

    _run_example()

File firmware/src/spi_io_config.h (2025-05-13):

/*
   Copyright 2020 Scott Bezek and the splitflap contributors

   Licensed under the Apache License, Version 2.0 (the "License");
   you may not use this file except in compliance with the License.
   You may obtain a copy of the License at

       http://www.apache.org/licenses/LICENSE-2.0

   Unless required by applicable law or agreed to in writing, software
   distributed under the License is distributed on an "AS IS" BASIS,
   WITHOUT WARRANTIES OR CONDITIONS OF ANY KIND, either express or implied.
   See the License for the specific language governing permissions and
   limitations under the License.
*/

#ifndef IO_CONFIG_H
#define IO_CONFIG_H

#include <SPI.h>

#if defined(__AVR_ATmega168__) || defined(__AVR_ATmega328P__)
  #define OUT_LATCH_PIN (4)
  #define _OUT_LATCH_PORT PORTD
  #define _OUT_LATCH_BIT 4

  #define IN_LATCH_PIN (5)
  #define _IN_LATCH_PORT PORTD
  #define _IN_LATCH_BIT 5

  #define OUT_LATCH(){\
    _OUT_LATCH_PORT |= (1 << _OUT_LATCH_BIT);\
    _OUT_LATCH_PORT &= ~(1 << _OUT_LATCH_BIT);\
  }
  #define IN_LATCH() {\
    _IN_LATCH_PORT &= ~(1 << _IN_LATCH_BIT);\
    _IN_LATCH_PORT |= (1 << _IN_LATCH_BIT);\
  }

  #define SPI_CLOCK 3000000

  #define BUFFER_ATTRS
#endif

#ifdef ARDUINO_ESP8266_WEMOS_D1MINI
  #define OUT_LATCH_PIN (D1)
  #define IN_LATCH_PIN (D2)

  #define OUT_LATCH() {digitalWrite(OUT_LATCH_PIN, HIGH); digitalWrite(OUT_LATCH_PIN, LOW);}
  #define IN_LATCH() {digitalWrite(IN_LATCH_PIN, LOW); digitalWrite(IN_LATCH_PIN, HIGH);}

  #define SPI_CLOCK 3000000

  #define BUFFER_ATTRS
#endif

#ifdef ESP32
  #include "driver/spi_master.h"
  #include "driver/spi_slave.h"

  #define LATCH_PIN (25)

  // Optional - uncomment if connecting the output enable pin of the 74HC595 shift registers
  // to the ESP32. You can otherwise hard-wire the output enable pins to always be enabled.
  // #define OUTPUT_ENABLE_PIN (27)

  #define PIN_NUM_MISO 39
  #define PIN_NUM_MOSI 32
  #define PIN_NUM_CLK  33

  // Note: You may need to slow this down to 3MHz if you're using a classic driver board;
  // the MIC5842 only officially supports up to 3.3MHz
  #define SPI_CLOCK 4000000

  #define BUFFER_ATTRS WORD_ALIGNED_ATTR

  // Note: must use HSPI to avoid conflict with ST7789 driver which uses VSPI
  #define SPLITFLAP_SPI_HOST HSPI_HOST
  #define DMA_CHANNEL 1


  spi_device_handle_t spi_tx;
  spi_device_handle_t spi_rx;

  spi_transaction_t tx_transaction;
  spi_transaction_t rx_transaction;


#endif

#if !defined(__AVR_ATmega168__) && !defined(__AVR_ATmega328P__) && !defined(ARDUINO_ESP8266_WEMOS_D1MINI) && !defined(ESP32)
#error "Unknown/unsupported board for SPI mode. ATmega328-based boards (Uno, Duemilanove, Diecimila), ESP8266 and ESP32 are currently supported"
#endif

#ifdef CHAINLINK
#define MOTOR_BUFFER_LENGTH (NUM_MODULES * 2 / 3 + (NUM_MODULES % 3 != 0) * 2)
#define SENSOR_BUFFER_LENGTH (NUM_MODULES / 6 + (NUM_MODULES % 6 != 0))
#else
#define MOTOR_BUFFER_LENGTH (NUM_MODULES / 2 + (NUM_MODULES % 2 != 0))
#define SENSOR_BUFFER_LENGTH (NUM_MODULES / 4 + (NUM_MODULES % 4 != 0))
#endif


BUFFER_ATTRS uint8_t motor_buffer[MOTOR_BUFFER_LENGTH];
BUFFER_ATTRS uint8_t sensor_buffer[SENSOR_BUFFER_LENGTH];

#ifdef __AVR__
// Define placement new so we can initialize SplitflapModules at runtime into a static buffer.
// (see https://arduino.stackexchange.com/a/1499)
void* operator new(__attribute__((unused)) size_t size, void* ptr) {
  return ptr;
}
#endif

#ifdef ESP32
void reset_latch(spi_transaction_t *trans) {
    digitalWrite(LATCH_PIN, LOW);
}

void latch_registers(spi_transaction_t *trans) {
    digitalWrite(LATCH_PIN, HIGH);
}
#endif

// Static buffer for SplitflapModules (initialized at runtime)
static char moduleBuffer[NUM_MODULES][sizeof(SplitflapModule)];

SplitflapModule* modules[NUM_MODULES];

#ifdef CHAINLINK
static const uint8_t MOTOR_OFFSET[] = {0, 0, 1, 2, 3, 3};
#endif

inline void initialize_modules() {
  for (uint8_t i = 0; i < NUM_MODULES; i++) {
    // Create SplitflapModules in a statically allocated buffer using placement new
#ifdef CHAINLINK
    modules[i] = new (moduleBuffer[i]) SplitflapModule(motor_buffer[MOTOR_BUFFER_LENGTH - 1 - i/6*4 - MOTOR_OFFSET[i%6]], i % 2 == 0 ? 0 : 4, sensor_buffer[i/6], 1 << (i % 6));
#else
    modules[i] = new (moduleBuffer[i]) SplitflapModule(motor_buffer[MOTOR_BUFFER_LENGTH - 1 - i/2], i % 2 == 0 ? 0 : 4, sensor_buffer[i/4], 1 << (i % 4));
#endif
  }
  
  memset(motor_buffer, 0, MOTOR_BUFFER_LENGTH);
  memset(sensor_buffer, 0, SENSOR_BUFFER_LENGTH);

  // Initialize SPI
#ifdef IN_LATCH_PIN
  pinMode(IN_LATCH_PIN, OUTPUT);
  digitalWrite(IN_LATCH_PIN, HIGH);
#endif

#ifdef OUT_LATCH_PIN
  pinMode(OUT_LATCH_PIN, OUTPUT);
  digitalWrite(OUT_LATCH_PIN, LOW);
#endif

#ifdef LATCH_PIN
  pinMode(LATCH_PIN, OUTPUT);
  digitalWrite(LATCH_PIN, LOW);
#endif
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

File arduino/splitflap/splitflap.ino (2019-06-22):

/*
   Copyright 2015-2016 Scott Bezek and the splitflap contributors

   Licensed under the Apache License, Version 2.0 (the "License");
   you may not use this file except in compliance with the License.
   You may obtain a copy of the License at

       http://www.apache.org/licenses/LICENSE-2.0

   Unless required by applicable law or agreed to in writing, software
   distributed under the License is distributed on an "AS IS" BASIS,
   WITHOUT WARRANTIES OR CONDITIONS OF ANY KIND, either express or implied.
   See the License for the specific language governing permissions and
   limitations under the License.
*/

/***** CONFIGURATION *****/

#define NUM_MODULES (12) //ON ESP32 you can control much more modules, but need to adapt SPI_IO_CONFIG accordingly
#define SENSOR_TEST false
#define SPI_IO true
#define REVERSE_MOTOR_DIRECTION false
#define BLUETOOTH true

// This should match the order of flaps on the spool:
const uint8_t flaps[] = {
  ' ',
  'a', 'b', 'c', 'd', 'e', 'f', 'g', 'h', 'i', 'j', 'k', 'l', 'm',
  'n', 'o', 'p', 'q', 'r', 's', 't', 'u', 'v', 'w', 'x', 'y', 'z',
  '0', '1', '2', '3', '4', '5', '6', '7', '8', '9',
  '.',
  ',',
  '\'',
};

/*************************/

#include "splitflap_module.h"

#if SPI_IO
#include "spi_io_config.h"
#else
#include "basic_io_config.h"
#endif

#if NEOPIXEL_DEBUGGING_ENABLED
#include <Adafruit_NeoPixel.h>
#endif


int recv_buffer[NUM_MODULES];

#if NEOPIXEL_DEBUGGING_ENABLED
Adafruit_NeoPixel strip = Adafruit_NeoPixel(NUM_MODULES, NEOPIXEL_PIN, NEO_GRB + NEO_KHZ800);
uint32_t color_green = strip.Color(0, 30, 0);
uint32_t color_red = strip.Color(100, 0, 0);
uint32_t color_purple = strip.Color(15, 0, 15);
uint32_t color_orange = strip.Color(30, 7, 0);
#endif

#ifdef __AVR__
#define FAVR(x) F(x)
#else
#define FAVR(x) x
#endif

#if defined(ESP32) && BLUETOOTH
#include "BluetoothSerial.h"
#if !defined(CONFIG_BT_ENABLED) || !defined(CONFIG_BLUEDROID_ENABLED)
#error Bluetooth is not enabled! Please run `make menuconfig` to and enable it
#endif

BluetoothSerial SerialBT;
#endif


void setup() {
  Serial.begin(38400);

  motor_sensor_setup();
  motor_sensor_io();

  Serial.print(FAVR("{\"type\":\"init\", \"num_modules\":"));
  Serial.print(NUM_MODULES);
  Serial.print(FAVR("}\n"));

#if NEOPIXEL_DEBUGGING_ENABLED
  strip.begin();
  strip.show();

  // Pulse neopixels for fun
  uint8_t vals[] = {0, 1, 3, 10, 16, 20, 24, 28, 28, 24, 20, 16, 10, 3, 1, 0};
  for (int16_t i = 0; i < 400; i++) {
    for (int j = 0; j < NUM_MODULES; j++) {
      int8_t index = i / 8 - j;
      if (index < 0) {
        index = 0;
      } else if (index > 15) {
        index = index % 16;
      }
      strip.setPixelColor(j, vals[index] * 2, vals[index] * 2, 0);
    }
    strip.show();
    delay(3);
  }
#endif

  for (uint8_t i = 0; i < NUM_MODULES; i++) {
    recv_buffer[i] = 0;
    modules[i].Init();
#if !SENSOR_TEST
    modules[i].GoHome();
#endif
  }

#if defined(ESP32) && BLUETOOTH
  SerialBT.begin("SplitFlap1"); //Bluetooth device name
  Serial.println("The device started, now you can pair it with bluetooth!");
#endif
}


inline int8_t FindFlapIndex(uint8_t character) {
    for (int8_t i = 0; i < NUM_FLAPS; i++) {
        if (character == flaps[i]) {
          return i;
        }
    }
    return -1;
}

bool was_idle = false;
bool was_stopped = false;
bool pending_no_op = false;
uint8_t recv_count = 0;

inline void run_iteration() {
    boolean all_idle = true;
    boolean all_stopped = true;
    boolean any_bad_timing = false;
    for (uint8_t i = 0; i < NUM_MODULES; i++) {
      any_bad_timing |= modules[i].Update();
      bool is_idle = modules[i].state == PANIC
#if HOME_CALIBRATION_ENABLED
        || modules[i].state == LOOK_FOR_HOME
        || modules[i].state == SENSOR_ERROR
#endif
        || (modules[i].state == NORMAL && modules[i].current_accel_step == 0);
      all_idle &= is_idle;
      all_stopped &= modules[i].current_accel_step == 0;
      if (i & 0b11) motor_sensor_io();
    }
    motor_sensor_io();

    if (all_idle) {
#if NEOPIXEL_DEBUGGING_ENABLED
      for (int i = 0; i < NUM_MODULES; i++) {
        uint32_t color;
        switch (modules[i].state) {
          case NORMAL:
            color = color_green;
            break;
#if HOME_CALIBRATION_ENABLED
          case LOOK_FOR_HOME:
            color = color_purple;
            break;
          case SENSOR_ERROR:
            color = color_orange;
            break;
#endif
          case PANIC:
            color = color_red;
            break;
        }
        strip.setPixelColor(i, color);
      }
      strip.show();
#endif

      while (Serial.available() > 0) {
        int b = Serial.read();
        switch (b) {
          case '@':
            for (uint8_t i = 0; i < NUM_MODULES; i++) {
              modules[i].ResetErrorCounters();
              modules[i].GoHome();
            }
            break;
          case '#':
            pending_no_op = true;
            break;
          case '=':
            recv_count = 0;
            break;
          case '\n':
              Serial.print(FAVR("{\"type\":\"move_echo\", \"dest\":\""));
              for (uint8_t i = 0; i < recv_count; i++) {
                int8_t index = FindFlapIndex(recv_buffer[i]);
                if (index != -1) {
                  modules[i].GoToFlapIndex(index);
                }
                Serial.write(recv_buffer[i]);
              }
              Serial.print(FAVR("\"}\n"));
              Serial.flush();
              break;
          default:
            if (recv_count > NUM_MODULES - 1) {
              break;
            }
            recv_buffer[recv_count] = b;
            recv_count++;
            break;
        }
      }

#if defined(ESP32) && BLUETOOTH
      while (SerialBT.available() > 0) {
        int c = SerialBT.read();
        switch (c) {
          case '@':
            for (uint8_t i = 0; i < NUM_MODULES; i++) {
              modules[i].ResetErrorCounters();
              modules[i].GoHome();
            }
            break;
          case '#':
            pending_no_op = true;
            break;
          case '=':
            recv_count = 0;
            break;
          case '\n':
              Serial.print(FAVR("{\"type\":\"move_echo\", \"dest\":\""));
              for (uint8_t i = 0; i < recv_count; i++) {
                int8_t index = FindFlapIndex(recv_buffer[i]);
                if (index != -1) {
                  modules[i].GoToFlapIndex(index);
                }
                Serial.write(recv_buffer[i]);
              }
              Serial.print(FAVR("\"}\n"));
              Serial.flush();
              break;
          default:
            if (recv_count > NUM_MODULES - 1) {
              break;
            }
            recv_buffer[recv_count] = c;
            recv_count++;
            break;
        }
      }
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

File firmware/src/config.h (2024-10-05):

#pragma once

#include <Arduino.h>

/***** CONFIGURATION *****/

// 1) Mode
#define SENSOR_TEST false

// 2) General Settings
#ifndef NUM_MODULES
// Set NUM_MODULES in platformio.ini instead when using ESP32/PlatformIO
#define NUM_MODULES (12)
#endif


// Whether to force a full rotation when the same letter is specified again
#define FORCE_FULL_ROTATION true

// Whether to use/expect a home sensor. Enable for auto-calibration via home
// sensor feedback. Disable for basic open-loop control (useful when first
// testing the split-flap, since home calibration can be tricky to fine tune)
#define HOME_CALIBRATION_ENABLED true

// 3) Flap Contents & Order
// This `flaps` array should match the order of flaps on your spools, with
// the first being the "home" flap.
//
// These are used for the built-in display, plaintext serial interface, and
// can be referenced by interactive controllers using the proto interface, but
// these are non-critical and only useful for interactive usage with the
// standard interfaces. (If you are using custom control software with the
// proto interface - you'll know if you are - you can ignore these since the
// proto interface uses integer indexes to reference flap positions).
//
// The conventions for these are as follows:
// - basic letters should be UPPER CASE
// - lower-case letters can be used to represent color blocks:
//   - g = green
//   - p = purple
//   - r = red
//   - w = white
//   - y = yellow

// Flap option 1: Legacy printed flaps (40 per module)
// #define NUM_FLAPS (40)
// const uint8_t flaps[NUM_FLAPS] = {
//   ' ',
//   'A', 'B', 'C', 'D', 'E', 'F', 'G', 'H', 'I', 'J', 'K', 'L', 'M',
//   'N', 'O', 'P', 'Q', 'R', 'S', 'T', 'U', 'V', 'W', 'X', 'Y', 'Z',
//   '0', '1', '2', '3', '4', '5', '6', '7', '8', '9',
//   '.',
//   ',',
//   '\'',
// };

// Flap option 2: v2 flaps (52 per module)
#define NUM_FLAPS (52)
const uint8_t flaps[NUM_FLAPS] = {
  ' ', 'A', 'B', 'C', 'D', 'E', 'F', 'G', 'H', 'I', 'J', 'K', 'L',
  'M', 'N', 'O', 'P', 'Q', 'R', 'S', 'T', 'U', 'V', 'W', 'X', 'Y',
  'Z', 'g', '0', '1', '2', '3', '4', '5', '6', '7', '8', '9', 'r',
  '.', '?', '-', '$', '\'', '#', 'y', 'p', ',', '!', '@', '&', 'w'
};

// Flap option 3: v2 flaps (limited 40-flap set using the first 40 flaps of the set)
// #define NUM_FLAPS (40)
// const uint8_t flaps[NUM_FLAPS] = {
//   ' ', 'A', 'B', 'C', 'D', 'E', 'F', 'G', 'H', 'I', 'J', 'K', 'L',
//   'M', 'N', 'O', 'P', 'Q', 'R', 'S', 'T', 'U', 'V', 'W', 'X', 'Y',
//   'Z', 'g', '0', '1', '2', '3', '4', '5', '6', '7', '8', '9', 'r',
//   '.',
// };

// Flap option 4: YOUR CUSTOM CHARACTER SET HERE!
// #define NUM_FLAPS (40)
// const uint8_t flaps[NUM_FLAPS] = {
//   <FILL THIS IN!>
// };


// 4) Hardware configuration and features
#ifndef SPLITFLAP_PIO_HARDWARE_CONFIG
  // Note: these values are only used in the Arduino IDE. For PlatformIO,
  // hardware configuration is set by the environment, in platformio.ini.
  #define SPI_IO true
  #define REVERSE_MOTOR_DIRECTION false
  #define NEOPIXEL_DEBUGGING_ENABLED true
  #define INA219_POWER_SENSE false
#endif

// 5) Board-dependent Default Settings

#if defined(__AVR_ATmega168__) || defined(__AVR_ATmega328P__)
  #if SPI_IO
  #define NEOPIXEL_PIN 6
  #else
  #define NEOPIXEL_PIN 3
  #endif
  #define MONITOR_SPEED 38400
#elif defined(__AVR_ATmega2560__)
  #define NEOPIXEL_PIN 5
  #define MONITOR_SPEED 38400
#elif defined(ARDUINO_ESP8266_WEMOS_D1MINI)
  #define NEOPIXEL_PIN (D8)
  #define MONITOR_SPEED 38400
#elif defined(ESP32)
  #define NEOPIXEL_PIN (13)
  #define MONITOR_SPEED 230400
#endif

/*************************/
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

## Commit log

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2015-10-26 remove back entirely, shrink idler, adjust enclosure for shortened right side and top
    [splitflap.scad]
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2015-10-26 Revert "Remove unnecessary bushing on right side (can use IR sensor against spool gear now)"
    This reverts commit d803c4d6d4403618ef8f8b68489414e39ca7f006.
    [splitflap.scad]
2015-10-26 Add some lateral slop to front window width, make front window overhang the theoretical correct position a bit
    [splitflap.scad]
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2015-11-01 shrinking spool and more based on real flap dimensions: smaller flap pin radius, less lateral slop
    [splitflap.scad]
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2015-11-14 Fix missing tab hole on bottom of right side
    Looks like an issue with the last tab hole being exactly aligned with the edge of the parent object it's being subtracted from. Fixes #1
    [splitflap.scad]
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2015-11-15 Lower top and bottom of front window
    Top of window needed to be lowered to retain flaps a little longer (fixes #2), and bottom of window needed to be lowered to allow fully-extended flaps to clear it (fixes #3). Window dimensions don't affect enclosure size, so that remains unchanged.
    [splitflap.scad]
2015-11-15 Initial progress on flap backstop
    Starting to design a flap backstop for issue #5: designed the shape of a new piece with m4 captive nut, but haven't cut slots for it in enclosure_bottom yet and haven't added it to 2d rendering.
    [splitflap.scad]
2015-11-15 Switch to using m4 bolts everywhere
    The main issue was the size of button head m4 bolts resulting in much larger adjacent holes that were nearly the diameter of the side_tab_width. Fixed this by parameterizing the side tabs to only occupy a fraction of the available space so that there can be more material left on either side when the bolt head holes are cut out. Fixes #6.
    There's still not too much material left between the bottom of the bolt head holes and the bottom of the enclosure (0.9 mm), so it may be worth extending the height of the enclosure in the future, though that would be backwards incompatible with previous enclosures.
    [splitflap.scad]
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2015-11-17 Fix missing tab hole on bottom of right side
    Fixes #1 (again) by adding back the extend_last_tab code that was incorrectly removed.
    [splitflap.scad]
2015-11-28 Add slot for bolt to act as flap backstop
    Allow for a bolt on the right side to stick inward and act as a flap backstop. I'm mostly guessing at the positioning and also made it a slot rather than a hole for the bolt to hopefully allow for some adjustment. Fixes #5 (but will reopen if it doesn't work out in practice).
    [splitflap.scad]
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2015-12-07 swap power and usb connectors to improve ground plane and avoid motor power crossing USB data lines
    [splitflap.kicad_pcb]
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2016-02-12 Move power connector and reset button; improves ground pour and should avoid motor ground current under the AVR/usb lines
    [splitflap.kicad_pcb]
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2016-05-08 Remove registration marks and supporting code
    The registration marks aren't really necessary, since the SVG coordinates are always absolute (with only the viewport being based on the shape). Even without the registration marks the component SVG files can be directly combined and everything will be aligned correctly.
    [projection_renderer.scad]
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2016-08-07 Working colored stl exporter
    Updated openscad models to use only the [0, 0, 0] color syntax (no more web named colors) and avoid nested colors. Finished initial export script that extracts all colors used in the model and then renders each color conditionally as a separate .stl file. Also generate a manifest.json file that encodes the mapping from stl filename to actual color information, which can be used for rendering the components with appropriate colors.
    [28byj-48.scad, splitflap.scad]
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2016-09-01 Add home-position hole in spool gear
    Create hole for IR reflectance sensor to detect. Fixes #9
    [splitflap.scad]
2016-11-17 Experiment with removing 5mm rod
    Replace 5mm rod with 2 M4 bolts attached to the left/right enclosure walls. Fixes #7.
    Removed the 2 outer spool bushings and updated dimensions to account for the thickness of an M4 nut instead.
    Widened the enclosure and inset the left and right sides to account for button head height; removed adjacent bolt head cutouts since left/right sides no longer touch adjacent sides.
    Now that adjacent enclosure bolt heads won't interact with each other, simplified the enclosure bolt layout (no more staggered bolts) and shortened the right side.
    [splitflap.scad]
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2017-09-19 Initial python implementation of controller
    Implemented new integer-based prototype of the splitflap module controller to avoid slow floating point math on the Arduino. Prototyped in python for easier testing and debugging.
    The main difference is that instead of tracking the position as a floating point flap-index (i.e. [0.0-40.0) for the 40 flaps) we now track everything in terms of integer motor steps, taking care to preserve the ability to handle tricky gear ratios like the ~63.684:1 commonly found in the 5V version of the 28byj-48 stepper. The other change is to do any "complex" math upfront (when commanding the module to move to a particular flap) so that the incremental updates can si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
    [splitflap.ino, splitflap_module.h]
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2017-10-16 Create a proper IDC connector footprint, move Expansion-In port to avoid PCB conflicts
    [splitflap.kicad_pcb, splitflap.sch]
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2018-02-07 Inline SplitflapModule methods
    Move the entirety of SplitflapModule to the .h file so that all methods can be inlined, for better performance. When driving all 12 modules at once, the overhead of method calls slows down the control loop frequency, so timing becomes less accurate and the stepper motors are more prone to skipping due to inconsistent step widths.
    Also applied a minor change to the startup LED animation, and conditions under which we refresh the status LEDs.
    [splitflap.ino, splitflap_module.h]
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2018-05-12 Shorten enclosure_length_right so design can fit within the Ponoko P1 safe zone
    [splitflap.scad]
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2018-05-22 Revert "Temporarily check in a snapshot of the build artifacts"
    This partially reverts commit 2a77d5ad65655cde89b440dbfa7e232b27ec23f0.
    [26a4ace46ae39933e6a48c7216e05c492121851603e5b7af95fbc77a7f3d4698.stl, 3cd8f4e35ca3e035304b257768e20abeb86d41b7f7ae6307dbdc77bff4ed98e5.stl, 5259f9e2da0ca43fbbd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]
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2018-05-29 Enable panelized 2d output for bulk laser-cutting
    Add panelization support to the projection renderer so that it can lay out the elements in a location for proper panelization when rendering for SVG output. Improved the previous N^2 redundant line removal to first bucket by rough slope-intersect values so that the N^2 comparisons only need to happen within a small bucket rather than over all lines in the entire document (which quickly becomes too slow).
    The design is panelized 2 per row (rotated 180 degrees and back-to-back).
    The `generate_2d.py` script now takes an optional `--panelize <number>` argument to generate a panelized SVG with the specified number of copies of the design. Since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
    [projection_renderer.scad, splitflap.scad]
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2018-07-14 Experimental updated connector design; fix Arduino code when home calibration is disabled
    [splitflap.scad]
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2018-08-02 JSON serial responses and example python code
    Make the Arduino only output single-line JSON objects via serial to make it easy for control software to parse.
    Also added some example python software which randomly picks words to display from a list of 4-letter animal names.
    Fixes #31
    [splitflap.ino, splitflap.py, splitflap_module.h]
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2018-08-03 Make electronics/generate_* scripts generic, WIP panelization
    Don't hardcode the splitflap.kicad_pcb path in the electronics generate_*.py scripts so they can be reused for the sensor board too.
    Some good progress on scripted panelization:
    - using Martin Furter's panelize.py to panelize KiCad pcb file (https://projects.borg.ch/electronics/kicad/panelize.html), with a small modification to make it handle "User" customized page sizes correctly
    - created `generate_panelize_config.py` as a way to programmatically generate a panelization config file from a few parameters (board origin, board size, rows, and columns)
    - generated panelization config includes drawing the panelized board outline and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
    [sensor.kicad_pcb]
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2018-08-07 Add shift register serial input pullup
    Add a 47k pull-up resistor so the sensor shift register's serial data input line isn't left floating when no expansion board is connected. Fixes #25.
    Also added a polarity indicator to the silkscreen near the power jack.
    [splitflap.kicad_pcb, splitflap.sch]
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2018-09-04 Replace AH1815 references with AH3391Q
    The AH1815 hall effect sensor won't work, as it samples the magnetic field too infrequently for the precision needed, as mentioned in https://github.com/scottbez1/splitflap/issues/29#issuecomment-418163631
    This replaces the AH1815 schematic/pcb module with a generic "hall_effect" module (since it seems most hall effect sensors have the same pinout and physical dimensions), and updates the schematic reference and BOM to specify AH3391Q as the preferred sensor. As noted in https://github.com/scottbez1/splitflap/issues/29#issuecomment-418234571 a number of other variants of hall effect sensor would also work, besides the AH3391Q, so the PCB silkscreen is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
    [sensor.kicad_pcb, sensor.sch]
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2018-09-04 Change sensor references to U100/P100 to avoid confusion with U1/P1 on controller PCB
    [sensor.kicad_pcb, sensor.sch]
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2018-09-11 Move R10 to maintain proper clearance from other resistors, minor silkscreen improvements
    [splitflap.kicad_pcb]
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2018-09-20 Simplify and strengthen inter-module connector
    Fixes #36. This eliminates the locking "tab" on the inter-module connector and instead makes the connector bracket slide into a slot in the front edge of the left/right side panels. Once the front panel is installed, the connector is locked in place so there's no need for the complexity of a locking tab.
    [splitflap.scad]
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2019-01-05 Move sensor_test into splitflap sketch
    This eliminates duplication of splitflap module IO code, which means you should now be able to run sensor tests in basic_io mode (previously sensor_test assumed spi_io mode). This is helpful for ESP8266 support (#55) so that latch pin configurations apply to sensor tests as well as regular run mode.
    Also, this fixes #50 by adding a new `REVERSE_MOTOR_DIRECTION` flag.
    [splitflap.ino, splitflap_module.h]
2019-01-05 Initial progress on ESP8266 support
    Refactored spi_io_config a bit so that the way the latch pins are toggled can be easily selected based on board type (AVR vs ESP8266).
    Add a yield() in the main loop on ESP8266 to avoid Soft WDT resets (though I still saw one in limited testing so there are likely some other issues to track down).
    Still haven't resolved the off-by-one-bit error with reading from the sensor shift register via SPI on ESP8266 (as noted in the github issue).
    Updates #55
    [basic_io_config.h, spi_io_config.h, splitflap.ino]
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2019-03-18 Add workaround for ESP8266 SPI read bit shift
    References #55. Basic ESP8266 support is mostly there. Still saw a Soft WDT reset after leaving this running for a while, so that's still a blocker.
    [spi_io_config.h]
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2020-04-18 Fix assert syntax conflict with newer OpenSCAD
    New OpenSCAD versions have official assert() syntax, which now causes a syntax error with the assert module. This renames assert to legacyAssert, but I'm still using legacyAssert (rather than the new assert() syntax) in order to continue supporting older versions of OpenSCAD.
    Fixes #80
    [assert.scad, splitflap.scad]
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2020-08-25 Extract splitflap code to own task, start showing real state on display (#87)
    - Created SplitflapTask and moved most code out of main.cpp
    - Renamed Display->DisplayTask
    - Added public `getState()` accessor to SplitflapTask to read the current state
    - Created SemaphoreGuard as a helper lock guard for FreeRTOS semaphore/mutexes - allows scope-based locked sections rather than explicit and error-prone lock/unlock calls
    - Implemented the most basic real display code showing splitflap state
    [splitflap_module.h, splitflap_task.cpp, splitflap_task.h]
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2020-09-10 Round motor window and CAD tweaks (#88)
    Rounds the corners of the motor window (r=5) for slightly more stiffness and a nicer fit + finish. With a radius of 5 mm this should still be a loose fit around the motor (at least according to the model). On the flat panel the spool retaining wall was moved to the X center of the window to clear the rounded corners while still maintaining its shared bottom edge.
    This also adjusts the lasercut panel so that the module connector pieces won't cut material out of the enclosure's left side. To do this the top and bottom pieces were moved down and the connectors were nested between the tabs in the top right corner. This keeps within the existing boundari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
    [splitflap.scad]
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2020-09-25 Font Rework and SVG Generation (#92)
    This PR overhauls how fonts are handled in the SCAD assembly, and adds a font generation feature for rendering SVG font files for cutting. The goal is to make it easy to generate custom split-flap fonts for desktop cutting machines (Cricut, Silhouette, etc.).
    Changes:
    * Added parametric font generation to SVG, for cutting your own letters (`generate_fonts.py` and `font_generator.scad`)
    * Letter rendering is now handled by a single function, with an argument to trim and position for either top or bottom
    * Letter geometry / position now matches flap geometry, so both `flap()` and `flap_letter()` can be called from the same point without additional tr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
    [flap_fonts.scad, font_generator.scad, splitflap.scad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]
2020-11-27 Thickness Fixes (+ 3.0 default) (#93)
    This PR fixes a few issues relating to panel thickness:
    - Spool width now accounts for flap width. If the calculated spool width is smaller than the flap width, the enclosure width and front opening do not shrink further. This also comments out the legacyAssert for spool width which is no longer needed.
    - Flap notch height and depth are now static and reflect the die-cut flap dimensions. The flap height can be set back to auto with the flap_notch_height_auto flag.
    - Enclosure side bolts are now positioned properly for all thicknesses
    - The enclosure vertical inset (distance between top/bottom of front and top/bottom pieces) now has a minimum value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
    [flap_dimensions.scad, splitflap.scad]
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2020-12-12 CAD Render Colors (#105)
    A number of changes to the assembly to make it easy to adjust the colors.
    First, the assembly color variations are now generated from a single base color. This means you can change the one 'assembly' color and still keep the color variation between parts. The scalars were calculated from the current values so everything should keep the same appearance as before. The etch color, similarly, has been broken out into a variable and can now be changed.
    Second, I've added variables for the hardware (nuts + bolts) and flap color. This allows you to change out the steel hardware for black oxide or swap the flaps from white to black. The letter color is calculated as th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
    [rough7380.scad, splitflap.scad]
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2020-12-12 Hall Effect Sensor Spacing and Jig (#101)
    This PR dynamically adjusts the hall effect sensor's height off of the PCB in the model based on its distance from the spool. The sensor will maintain the same relative distance from the spool as the model is changed and throw an error if its distance from the PCB exceeds the max length of the sensor's leads (per the datasheet). I also created a small lasercut jig that fits between the PCB and the sensor to aid in soldering.
    Using your v0.5 sensor assembly video as reference, I set the spool offset to 0.7 mm which corresponds to a distance of 5.8 mm from the PCB. Note that this PR has a conflict with #100 that will need to be resolved, as the new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
    [pcb.scad, splitflap.scad]
2020-12-12 Sensor PCB Case (#104)
    As with the flap case (#103), while I'm waiting for the enclosures to be finished I have a bunch of assembled sensor PCBs sitting around. This is a little dangerous since the hall effect sensors stick out from the board and can be accidentally bent out of position. So I designed a 3D printed case for them to safely sit in until the modules can be assembled.
    The design has a `cases_per_row` parameter for generating multiple cases in one design, as well as a `dual_rows` parameter that mirrors a second row along the back for double the number of PCB spots:
    [pcb.scad, pcb_case.scad]
2020-12-13 Spool Fitment Adjustments (#107)
    This PR makes a few minor adjustments to how the spool assembly fits together.
    First and most importantly, the `spool_tab_clearance` value, which affects the fitment between the spool struts and the spool end pieces, has been changed from a slight clearance / free fit (`0.1 mm`) to a slight interference fit (`-0.02 mm`). This was an oversight - the spool, as designed, needs to be an interference fit otherwise the spool endpieces fall right off. Mea culpa.
    The spool struts themselves, as well as the spool retaining wall, will keep their `0.1 mm` clearance value so they'll fit together smoothly. This also gives you a little bit of wiggle room when trying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
    [splitflap.scad]
2020-12-13 Organize 3D printed tools (#108)
    Collects all of the 3D printed tool designs in a subfolder to try and keep the CAD files at least somewhat organized. Also fixes a bug with the optional PCB rendering in the PCB case design and adds a section to the README about these designs.
    [flap_container.scad, pcb_case.scad, punch_jig.scad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]
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2020-12-24 Zip Ties for Cable Management (#109)
    Adds holes for cable management zip ties into the left side of the enclosure: one pair underneath the sensor PCB for wires exiting downwards (PCB behind module) and one pair above the motor for wires exiting upwards (PCB mounted on top of module(s)). The goal is to prevent the wires from bending outwards and getting tangled in the moving spools of adjacent modules.
    These are sized to work with your typical 2.5 mm wide mini zip ties.
    [splitflap.scad]
2020-12-27 Laser Layout Mirror Option (#106)
    This adds the option to mirror the 2D laser-cut design so that the outside faces are facing 'up' / towards the laser when cut. This is useful for materials with a special finish on only one side like Ponoko's matte black acrylic, which is cut with the matte finish facing towards the laser.
    The mirroring can be set with the render_2d_mirror flag, or with the --mirror option in the generate_2d.py script.
    With the addition of the alignment indicators (PR #111) I think we've reached the point where it no longer makes sense to mirror the individual etched portions. Instead, I've updated the etch function to prevent rendering the laser etches if the mirror o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
    [splitflap.scad]
2021-01-27 CAD: Move flap thickness slop to spool slop (#114)
    This increase was a mistake. The difference in thickness (0.2 on either side) should have been added to the *spool* slop instead of the flap width slop, as the inner width of the spool (flap_width_slop) was not affected by the thickness parameter, while the outer width of the spool (spool_width_slop) *was*. This commit corrects that oversight.
    This reverts commit a68fc988bc73c146c28ed1dc2c8e02c990d5ab93 (squashed as part of 7be69dbeb4fb7c1aa4b29027eb3e49a9b121c6a2).
    On my test display the spool will sometimes stall while rapiding. It appears that this is caused by imperfect assembly of the spool and the flaps sliding sideways, causing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
    [splitflap.scad]
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2021-02-28 CAD: Tweak Spool Fitment Values (#122)
    On my latest order from Ponoko (3 mm acrylic) the spool struts are still loose and will need to be glued. This increases the interference a bit more (+ 0.04 mm) to hopefully reach a point where the struts will fit into the spool and hold there by friction alone.
    Also increased is the flap width slop, in a reversion to the change from #114. On my order based around f4e7714 the flaps do *fit* and swing but it's tight - a little bit of misalignment with the spool end pieces or burrs on the parts will cause them to bind. And after gluing the end pieces in place not *perfectly* parallel (+/- 0.15 mm across ~48 mm diameter) that's exactly what has happened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
    [splitflap.scad]
2021-02-28 Add more tolerance to cavity_top_allowance (#124)
    I think the default should add a bit more tolerance to the hight of the cavity. I just printed it and it's about 3 cards too low for me. Perhaps the vinyl added unexpected thickness. I think 3mm extra should be good.
    [flap_container.scad]
2021-02-28 CAD: Increase Motor Clearance (#121)
    Increases the clearance between the motor chassis and the right outside wall of the previous module. Also refactors this variable from 'slop' to 'clearance' for a better description of what it represents.
    This is still playing a bit of catch-up from the thickness change (#93). In the previous release where the thickness parameter was set to 3.2 mm but the manufactured panels were actually 3.0 mm thick, there was extra space between the motor chassis and the previous module. This change adds that additional 0.4 mm of clearance back as part of the motor clearance variable.
    The additional clearance also makes the widths between the two designs approxim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
    [splitflap.scad]
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2021-03-09 Add Chainlink Driver (#132)
    There's a lot going on here, but it's time to start merging some of this to master to avoid diverging too far on a branch.
    - Adds new Chainlink Driver electronics design
    - Adds rough firmware support for Chainlink Driver electronics (ESP32-specific changes), controlled by a `#define CHAINLINK`. General ESP32 support should mostly still work, but no guarantees
    - Adds KiCad 5 support to CI scripting/automation, including hacky 3d rendering
    - Also adds the extremely experimental Mega 2560 electronics design (and some firmware tweaks related to it), called `moduleDriver` (I'll clean this up in future commits)
    - `espShifter` is the vestigial remains of a prior i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
    [chainlinkDriver.kicad_pcb, chainlinkDriver.sch, espShifter.kicad_pcb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]
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2021-03-16 Sensor PCB Tweaks (#135)
    Fixes the sensor PCB `Edge.Cuts` layer continuity and moves the commit silkscreen off of the pads.
    These commits were cherry-picked from PR #97
    [sensor.kicad_pcb]
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2021-03-24 Classic controller PCB Tweaks (#97)
    #### Changes + Additions:
    * Added an LED solder disconnect jumper (NC), in case the user wants to disable the always-on LEDs
    #### Improvements:
    * Rotated capacitor C1 so that its polarity matches C3
    * Trimmed + added a notch indicator to the 74HC165 footprint's silkscreen
    * Rotated all silkscreen text vertically for easier readability
    * Added silkscreen outlines to Arduino ports on bottom
    #### Bugfixes:
    * Cleaned up excess / overlapping tracks (from grid / snapping issues)
    There should be no changes to the core PCB functionality.
    [sensor.kicad_pcb, splitflap.kicad_pcb, splitflap.sch]
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2021-03-25 Fix firmware compilation for Uno (#140)
    These were removed as part of the chainlink driver PR (#132) and the consolidation to 'LATCH_PIN' for the ESP32.
    [spi_io_config.h]
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
